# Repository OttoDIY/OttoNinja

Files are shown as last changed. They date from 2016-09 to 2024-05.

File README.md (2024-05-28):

# Otto Ninja Robot Arduino Libraries




This repository has the main [Otto Ninja robot](https://www.ottodiy.com/ninja) libraries for ESP compatible boards.

## Compatible Hardware

- Designed to work with ESP8266 boards, but most of the code could be adapted to other microcontrollers.

You will need to [add the ESP8266 to your Arduino IDE](https://randomnerdtutorials.com/how-to-install-esp8266-board-arduino-ide/)

:star: Star us on GitHub; it helps!

## Installation:

You will need the [Arduino IDE on your computer](https://www.arduino.cc/en/software)

1. [Download Otto Ninja libraries here](https://github.com/OttoDIY/OttoNinja/archive/master.zip)
2. Open the Arduino IDE and navigate to Sketch > Include Library > Add .ZIP Library...
3. Navigate to .zip file location that you just downloaded and open it.
4. You will see in the bottom black area a message that it has been installed. 
5. To verify they are properly installed, go to Sketch > Include Library menu. You should now see the library at the bottom of the drop-down menu.

## Example:

You can find codes in File > Examples > OttoNinja.

*For more details or other ways to [install libraries, visit this link](https://www.arduino.cc/en/Guide/Libraries) 

*For the LED matrix, you will need the [Adafruit LED Backpack library and all the dependencies](https://github.com/adafruit/Adafruit_LED_Backpack/archive/refs/heads/master.zip) just do the exact same installation steps.

*For the OLED display, you will need the [U8g2 libraries](https://github.com/olikraus/u8g2/archive/refs/heads/master.zip)

## Uploading:

For the firmware code to remote control Ninja via the [Remote XY mobile App](https://remotexy.com), select NodeMCU 1.0 as the board.

1. Connect the ESP board using the USB cable to your computer.

2. [Upload this code](https://github.com/OttoDIY/OttoNinja/blob/master/examples/App/OttoNinja_APP/OttoNinja_APP.ino) 
3. [Download the app to your phone](https://remotexy.com/en/download/)
4. Open the app and press + Add new device.
5. Select the WiFi point.
6. Select "OTTO NINJA" from the options.
7. The password is 12345678.

(Make sure to have wifi disconnected from other networks) and power the robot with a battery all the time.

## How to Contribute:
Contributing to this software is warmly welcomed.
1. Test it, and if you find any problems, then post an issue.
2. Help us solve the issues or other bugs.
3. Improve and optimize the current libraries.
You can do this [basically by forking](https://help.github.com/en/articles/fork-a-repo), committing modifications, and then [pull a request](https://help.github.com/en/articles/about-pull-requests). 

Thanks for your contribution, and welcome to the [Otto DIY community](https://www.ottodiy.com/community)

## License: CC-BY-SA
You can use all resources of Otto for free, but Otto DIY website must be included in any redistribution, and remixes must keep the CC-BY-SA license. In open source, the idea is that more people can have access; therefore, if you copy or remix Otto, you must also release it under the same open license, which means you must also release all files to the public.

<br /><span xmlns:dct="http://purl.org/dc/terms/" property="dct:title">Otto DIY</span> by <a xmlns:cc="http://creativecommons.org/ns#"  property="cc:attributionName"> [www.ottodiy.com](http://www.ottodiy.com) </a> is licensed under a <a rel="license" href="http://creativecommons.org/licenses/by-sa/4.0/">Creative Commons Attribution-ShareAlike 4.0 International License</a>.

Thanks to [Sebastian Coddington](https://github.com/SebastianCoddington) for this project.

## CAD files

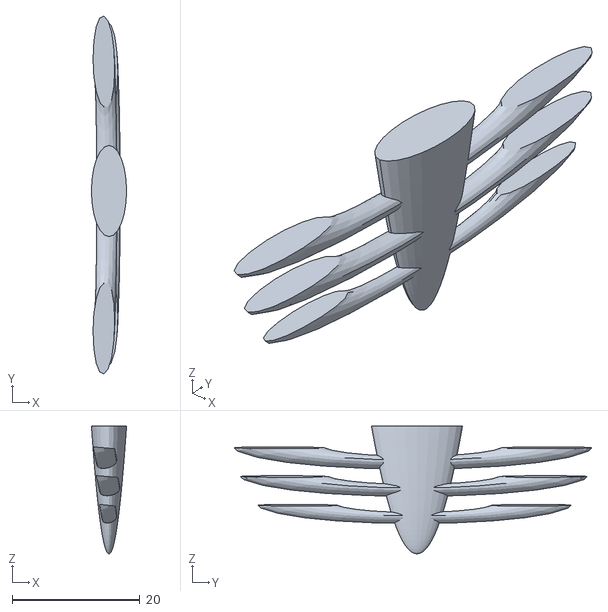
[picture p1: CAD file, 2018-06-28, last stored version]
3D print/accessories/Otto_RibCage.stl
5.50 x 56.0 x 20.0

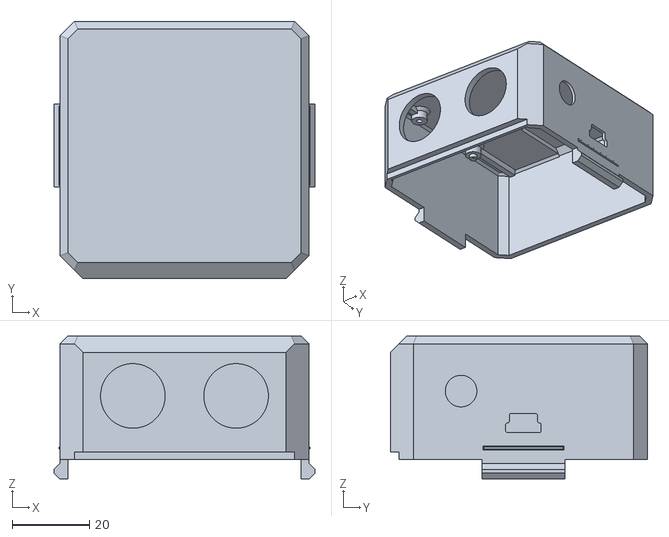
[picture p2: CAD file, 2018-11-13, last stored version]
3D print/OttoDIY+_head_v08.stl
67.6 x 66.7 x 37.0

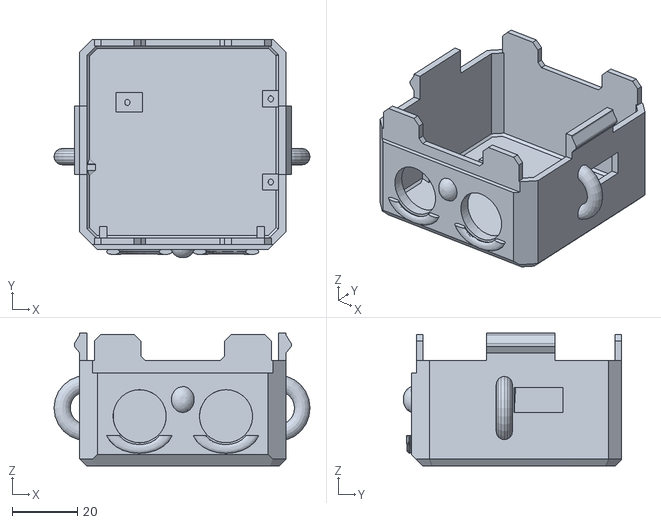
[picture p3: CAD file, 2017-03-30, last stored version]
OTTO_V02_BOM_STP_STL/Otto_Head+Face_Ears.stl
78.5 x 66.8 x 40.7

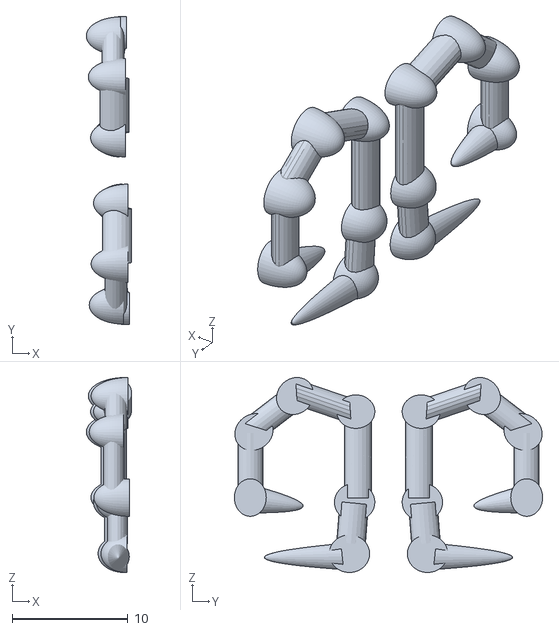
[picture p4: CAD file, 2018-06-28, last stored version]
3D print/accessories/Otto_BoneyHands.stl
3.92 x 26.6 x 16.8

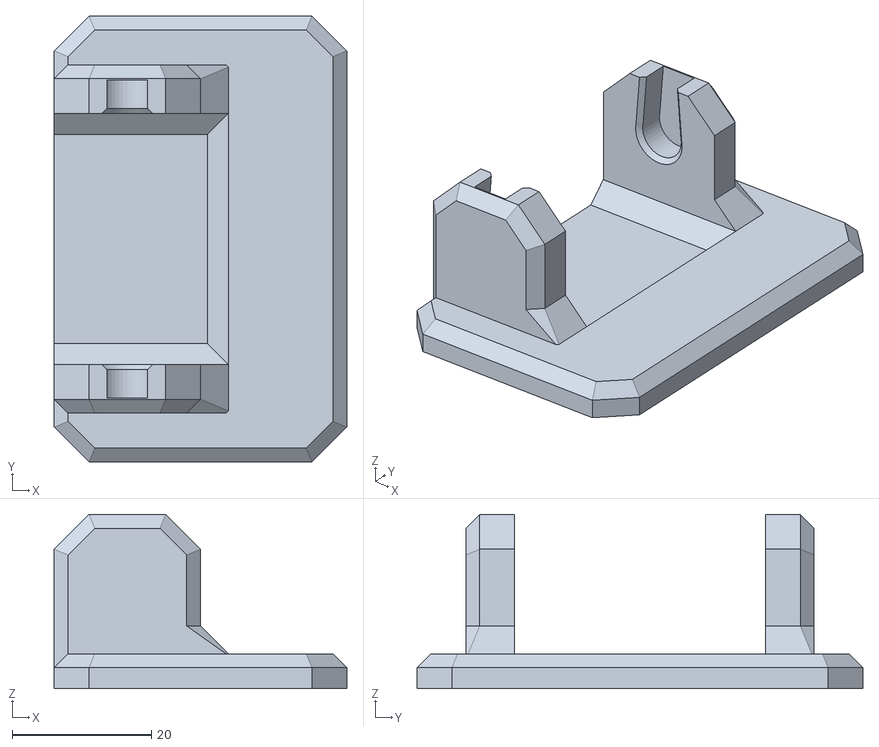
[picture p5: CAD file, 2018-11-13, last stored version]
3D print/OttoDIY+_foot_v08.stl
42.0 x 64.0 x 25.0

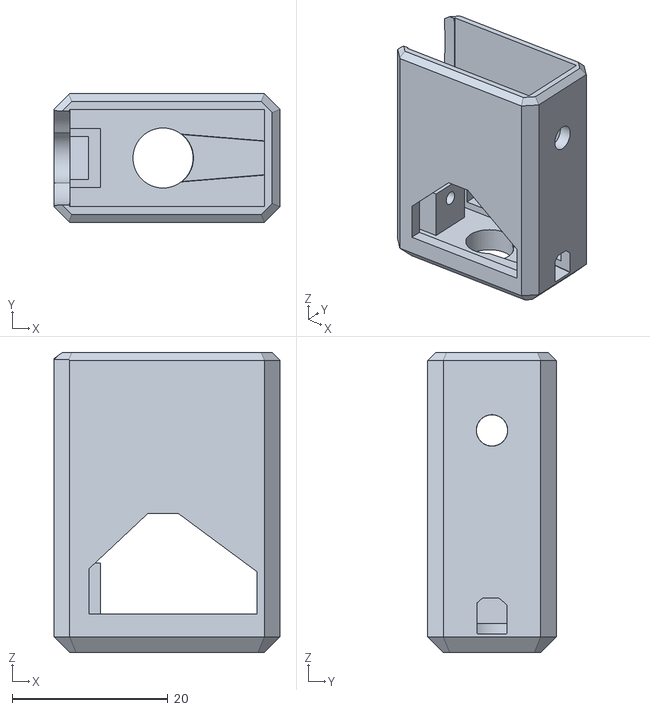
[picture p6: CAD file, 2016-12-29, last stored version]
OTTO_V02_BOM_STP_STL/OTTO_leg_v4.stl
29.0 x 16.5 x 38.5

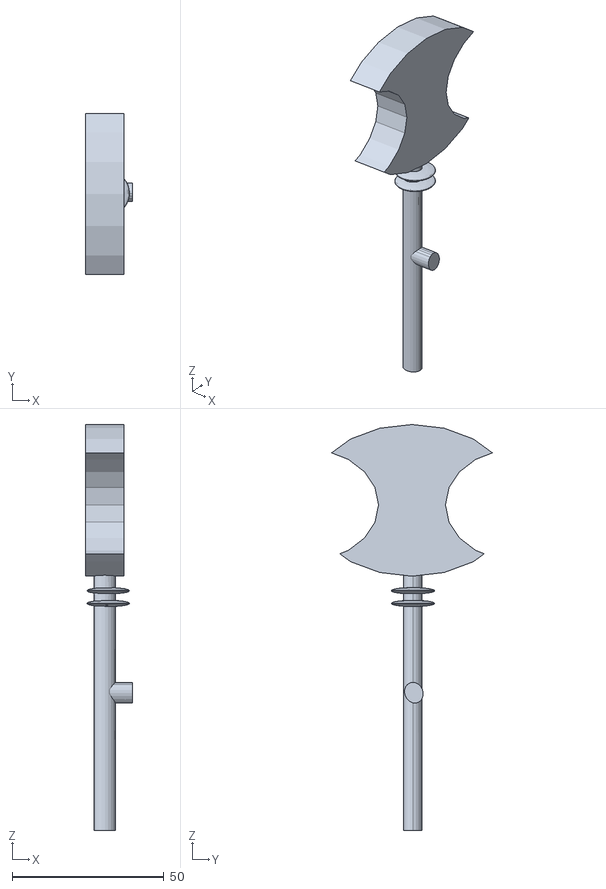
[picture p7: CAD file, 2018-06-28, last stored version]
3D print/accessories/Otto_MedievalAxe.stl
15.5 x 53.0 x 133.8

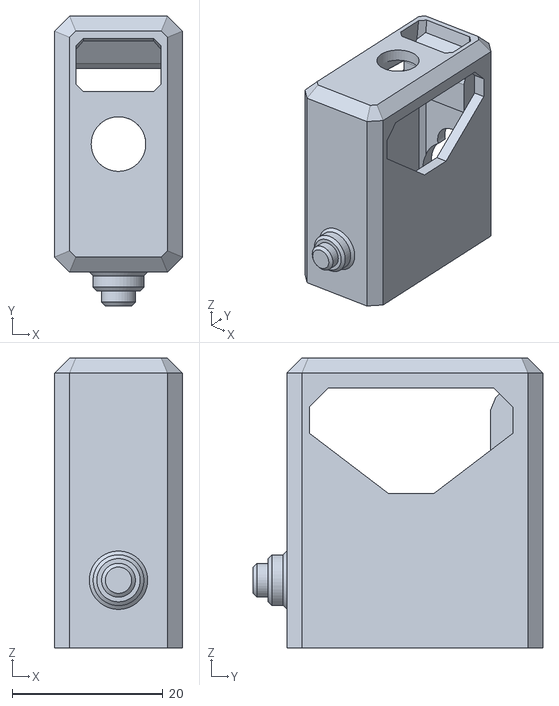
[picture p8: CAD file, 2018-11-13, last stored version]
3D print/OttoDIY+_Leg_v08.stl
17.0 x 38.5 x 38.5

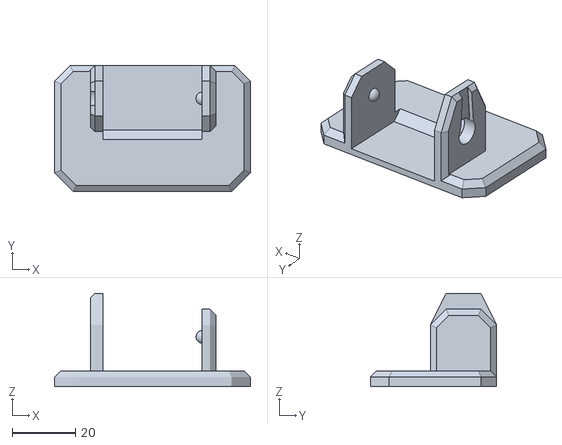
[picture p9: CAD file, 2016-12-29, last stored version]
OTTO_V02_BOM_STP_STL/OTTO_footR_v3.stl
62.0 x 40.0 x 29.5

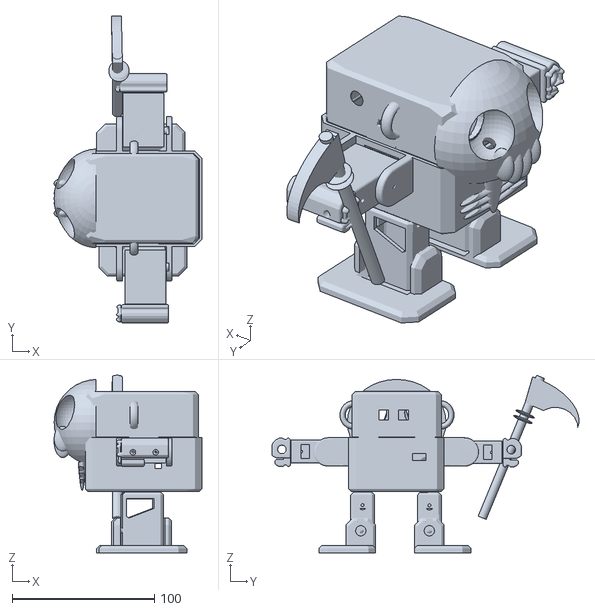
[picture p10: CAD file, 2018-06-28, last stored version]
3D print/accessories/Otto_Halloween_remix_Tinyplans_minion.stl
104.0 x 216.1 x 125.0

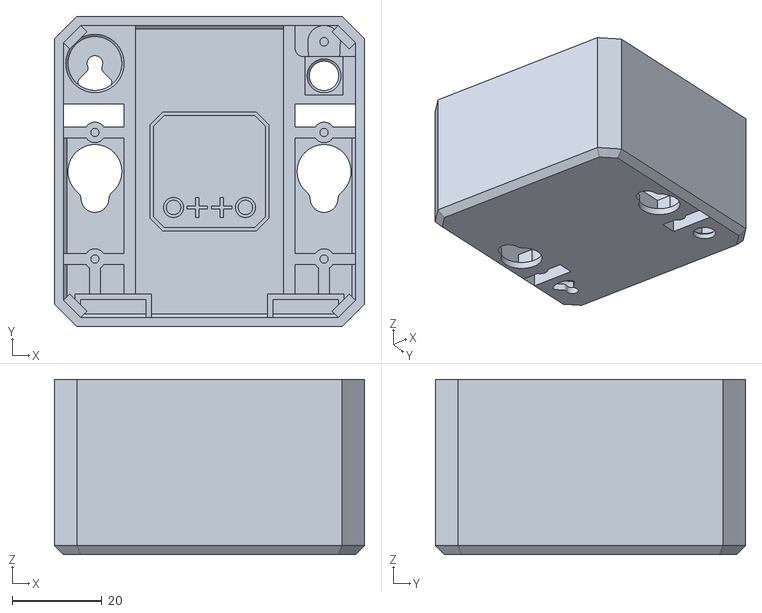
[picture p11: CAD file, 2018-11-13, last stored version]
3D print/OttoDIY+_body_v08.stl
69.0 x 69.0 x 39.0

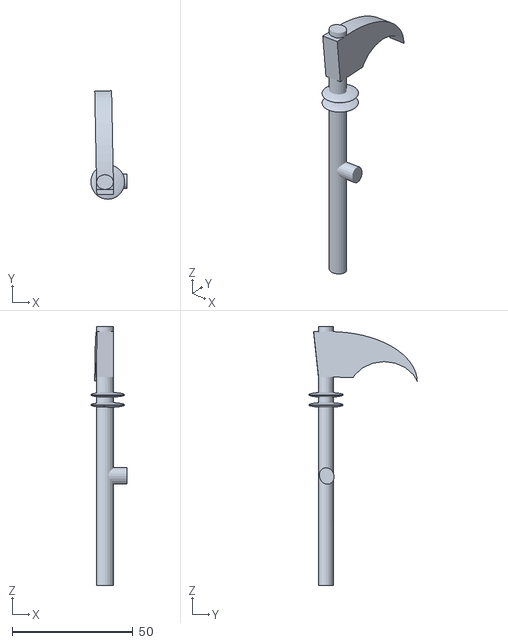
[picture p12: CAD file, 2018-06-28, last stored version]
3D print/accessories/Otto_Scythe+Connect.stl
15.0 x 45.0 x 107.4

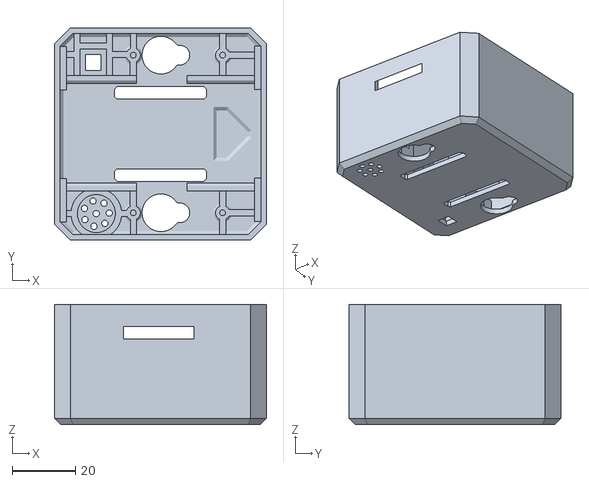
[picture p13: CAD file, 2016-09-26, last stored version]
OTTO_V02_BOM_STP_STL/OTTO_body_v3.stl
67.0 x 67.0 x 38.0

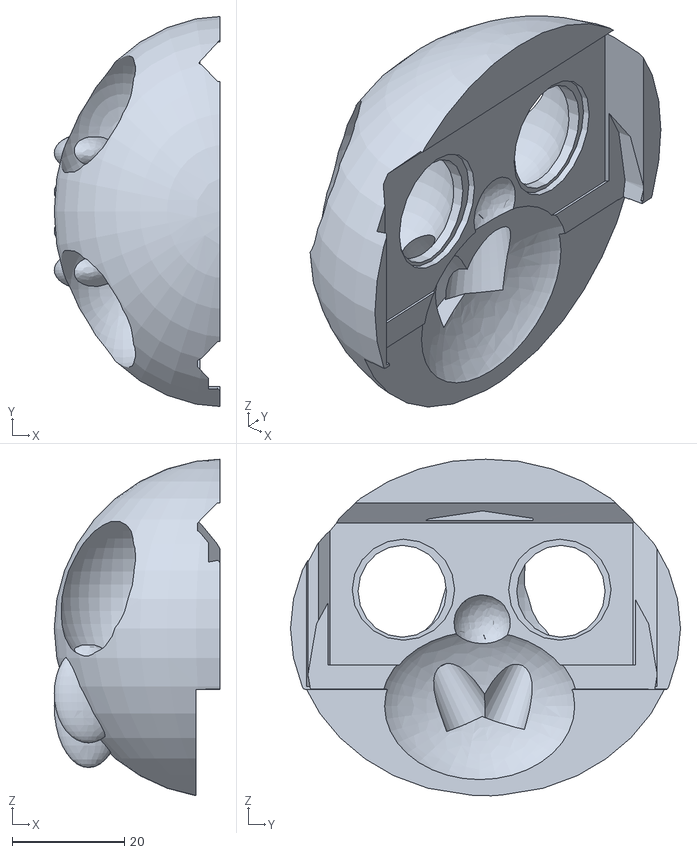
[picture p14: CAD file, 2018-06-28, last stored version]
3D print/accessories/Otto_Skull.stl
29.5 x 69.5 x 60.0

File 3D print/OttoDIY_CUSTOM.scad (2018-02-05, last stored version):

// Part to print
part="all"; // [all:Preview Bot,head:Head,body:Body,leg:Leg,foot_left:Left Foot,foot_right:Right Foot]

// Brain type (hole pattern in head)
brain_type="nano_shield"; // [nano_shield:Stock (Arduino Nano + Servo Shield),nano_proto:Arduino Nano + Proto board,uno_shield:Arduino Uno + Servo Shield,uno:Arduino Uno (and wires)]

// Servo Type for hip
servo_type_hip="sg90"; // [sg90:SG90 (nylon gear micro servo),mg90s:MG90S (metal gear micro servo)]

// Servo Type for ankle
servo_type_ankle="sg90"; // [sg90:SG90 (nylon gear micro servo),mg90s:MG90S (metal gear micro servo)]

// Body Width (Head width is based off this)
body_width=67; // [67:200]

// Body Depth (Head depth is based off this)
body_depth=68; // [68:200]

// Body Height
body_height=38; // [20:200]

// Head Height
head_height=34; // [20:200]

// Body Shell Thickness
body_thickness=1.75; // [0.25:0.25:8]

// Head Shell Thickness
head_thickness=2; // [0.25:0.25:8]

// Nose Diameter (6 = Small Toggle Switch)
nose_diameter=6; // [0:24]
// Vertical distance between center of eyes and nose
nose_distance=15; // [-8:190] 

// Brain Screw Size (2 = Stock)
brain_screw_size=2; // [2:5]

// Make Brain Screw thru Skull
brain_screw_thru=0; // [1:Yes,0:No]

// Solid leg
leg_solid=0; // [1:Yes, solid,0:No, my printer doesn't like those overhangs]

/* [Hidden] */
part_clearance=0.25;

arduino_holes=[[-27,-7],[-27,20.9],[25.2,26.1],[23.825,-22.25]];
proto_holes=[[27,-10],[-17.9,-10],[26,25.5],[-17.7,25.5]];

print_part();

module print_part() {
  warnings()
    draw_part();
}

module draw_part() {
  if(part=="head")
    head();
  else if(part=="body")
    body();
  else if(part=="leg")
    leg();
  else if(part=="foot_left")
    foot();
  else if(part=="foot_right")
    mirror([1,0]) foot();
  else if(part=="all")
    rotate([0,0,-90]) otto();
}
module otto() {
  head(move=1);
  body(move=1);
  mirrory() {
    translate([0,body_width/2-33.5,0])
    {
      mirror([1,0]) foot(move=1);
      translate([0,24,-1]) mirror([0,0,1]) leg(move=0);
    }
  }
}
function brain_type_text() = (
  brain_type=="nano_shield"?"Arduino Nano + Servo Shield":(
  brain_type=="uno_shield"?"Arduino Uno + Servo Shield":(
  brain_type=="nano_proto"?"Arduino Nano + Proto board":"Unknown")));
module warnings() {
  if(brain_type=="nano_shield")
  {
    if(body_width<67)
      error(str("If ",brain_type_text()," is used, Body Width must be >= 67!"));
    else if(body_depth<67)
      error(str("If ",brain_type_text()," is used, Body Depth must be >= 67!"));
    else children();
  } else if(brain_type=="uno_shield"||brain_type=="uno")
  {
    if(body_width<81)
      error("If Arduino Uno is used, body width MUST be greater than 81!");
    else children();
  } else children();
}
module error(s) {
  echo(str("***ERROR*** ",s));
  rotate([0,0,-45])
        rotate([80,0,0]) color("red") text(s);
}
module body(dims=[body_depth-1,body_width,body_height]) {
  left=dims[0]/-2; // -33.5
  botm=dims[1]/-2; // -33.5
  right=dims[0]/2; // 34
  servozoff=servo_type_hip=="sg90"?2:0;
  *#import("Otto_DIY/files/OTTO_body_v3.stl");
  mirrorx(0.4) mirrory(0.25) translate([left+body_thickness,botm+body_thickness+13.775,body_thickness]) {
      cube([dims[0]/2-9,2.5,12.4]);
      translate([0,2.5,12.39]) rotate([90,0,90]) mirror([1,0]) linear_extrude(dims[0]/2-9,convexity=10) polygon([[0,0],[1.2,0.825],[2.5,0.825],[2.5,0]]);
  }
  mirrory() mirrorx() translate([left+body_thickness-.01,botm+6,dims[2]-16]) difference(){
    cube([2,13.7,5]);
    translate([0,-.01]) rotate([0,41]) cube([3,13.72,5]);
  }
  mirrory() for(x=[0,28.2]) translate([x-9.5,botm+body_thickness,body_thickness]) difference() {
    union(){
      cube([2,13.775,6.18-servozoff]);
      translate([0.98,6.85,0]) cylinder(d1=5.7,d2=4.4,h=0.85,$fn=30);
      translate([0.98,6.85,0.84]) cylinder(d=4.4,h=5.35-servozoff,$fn=40);
    }
      translate([0.98,6.85,-.01]) cylinder(d=1.9,h=7,$fn=20);
  }
  for(mx=[0,1],my=[0,1]) mirror([mx,0]) mirror([0,my]) translate([mx?-11:0,0])
  translate([left+body_thickness+22.2,botm+body_thickness,body_thickness]) difference() { union() {
      if(!mx&&!my)
        translate([-10.7,6.61])
          cylinder(d=16,h=6.25-servozoff,$fn=50);
      else if(!mx&&my)
        translate([-17.5,0,.01]) cube([11.9,13.2,6-servozoff]);
      translate([-1-(left+33),5.64,0]) mirror([1,0]) cube([(mx?-22:-12)-left,2,6.1-servozoff]);
    }
    if(!mx&&!my)
      translate([-10.72,6.61,-.01]) cylinder(d=12,h=6.27,$fn=40);
    else if(!mx&&my)
      translate([-15.9,5,-.01]) {
        cube([8.35,8.2,7]);
        translate([0,-6]) cube([8.35,4,7]);
      }
  }
  difference() {
      translate([left,botm,0]) box_chamfer(dims,ch=2,chvx=5,chvy=5);
//    translate([left+1.75,botm+1.75,2]) box_chamfer([dims[0]-3.5,dims[1]-3.5,dims[2]],ch=1,chvx=4,chvy=4,inside=1);
    translate([left+body_thickness,botm+body_thickness,2]) box_chamfer([dims[0]-body_thickness*2,dims[1]-body_thickness*2,dims[2]],ch=1,chvx=4,chvy=4,inside=1);
    translate([0,0,-1]) linear_extrude(10,convexity=10) {
      mirrory() {
        translate([.1,botm+8.5]) circle(d=12,$fn=30);
        translate([6,botm+8.5]) circle(d=servo_type_hip=="mg90s"?6.5:7,$fn=20);
        offset(-1) offset(1)
        translate([-14.5,-15]) square([29,4]);
      }
      translate([left+9,-botm-13.5]) square([5.2,5.2]);
      translate([left+12.8,botm+8.35]) {
        circle(d=2,$fn=20);
        for(r=[2:360/7:359]) rotate([0,0,r]) translate([4.1,0]) circle(d=2,$fn=20);
      }
    }
    mirrory() translate([-11.7,right-body_thickness-.51,dims[2]-11]) {  cube([22.35,body_thickness+0.6,4]);
      translate([0,body_thickness+.02,4.1]) rotate([-35,0]) mirror([0,0,1]) mirror([0,1,0]) cube([22.35,4,5.4]);
    }
  }
}
module head(dims=[
    body_width-(body_thickness+part_clearance)*2,
    body_depth-(body_thickness+part_clearance)*2,
    head_height],brain_type=brain_type,head_thickness=head_thickness,move=0) {
  left=dims[0]/-2; // -31.5
  botm=dims[1]/-2; // -32.25
  right=dims[0]/2; // 31.5
  translate(move?[0,0,body_height+head_height-3]:[]) rotate(move?[180,0,-90]:[]) {
    //#import("Otto_DIY/files/OTTO_head_v3.stl");
    difference(){
      translate([left,botm,0]) box_chamfer(dims,ch=2,chy1=3.5,chvx=5.5,chvy=4);
      translate([left+head_thickness,botm+head_thickness+1.501,head_thickness]) box_chamfer([dims[0]-head_thickness*2,dims[1]-head_thickness*2-1.5,dims[2]],ch=1,chvx=2.75,chvy=2.75,inside=1);
      translate([left,botm-.01,dims[2]-3.8]) cube([dims[0],1.5,10]);
      for(x=[-13.25,13.25])
        translate([x,botm-.01,15]) rotate([-90,0]) cylinder(d=16.5,h=4,$fn=50);
      brain_holes(brain_type,top=dims[1]/2-20,right=dims[0]/2);
      translate([-5.6,-29.555,3.75]) {
        translate([11.25,0]) rotate([-90,0]) rotate([0,0,180]) intersection() {
          box_chamfer([11.3,7.6,2],ch=0,chvx=1.6,chvy=1.6);
          translate([0,0,-.8]) box_chamfer([11.3,7.6,4],ch=1.6,chvx=0,chvy=0);
          
        }
      }
      if(nose_diameter>0&&dims[2]-(nose_diameter/2+nose_distance)>18)
      {
        translate([0,botm-.01,15+nose_distance]) rotate([-90,0]) cylinder(d=nose_diameter,h=head_thickness+2.02,$fn=30);
      } else echo(str("Warning: Hiding nose."));
    }
    // tabs
    mirrorx() translate([-left-2,-9.25,dims[2]]) rotate([-90,0]) mirror([0,1,0]) linear_extrude(21,convexity=10) polygon([[0,0],[0,8.4],[1.98,8.4],[4.1,6.3],[4.1,4.2],[2,2.5],[2,0],]);
    mirrory(0.75) mirrorx(0) translate([left+4.5,botm+1.5,dims[2]]) rotate([90,0]) mirror([0,0,1]) linear_extrude(2) polygon([[0,0],[0,6],[2,8],[12,8],[14,6],[14,1.5],[15.5,0]]);
    brain(brain_type=brain_type,top=dims[1]/2-20,right=dims[0]/2);
  }
}
module leg(move=0) {
  bo=servo_type_ankle=="sg90"?0:(
    servo_type_ankle=="mg90s"?1.6:0);
  translate(move?[0,24,-40]:[]) rotate([0,0,0]) union(){
  //#import("Otto_DIY/files/OTTO_leg_v4.stl");
  difference() {
    translate([-14.5,-8.25,0]) {
      intersection() {
        cube([29,16.5,38.5]);
        union(){
          box_chamfer([29,16.5,20],2);
          translate([0,0,38.6]) mirror([0,0,1]) box_chamfer([29,16.5,20],1.25,chvx=2,chvy=2);
          *translate([1,1,30])
            box_chamfer2([29-2,16.5-2,7],2);
        }
      }
    }
    translate([-12.5,-6.25,4.25]) cube([25,12.5,50]);
    translate([12,-3,5]) cube([6,6,7.5]);
    translate([0.5,0,2.6-(servo_type_hip=="mg90s"?0:1)]) rotate([0,0,90]) {
      linear_extrude(3.4) 
        polygon([[-3.1,0],[-2,20],[2,20],[2.8,0]]); 
      translate([0,0,-3.01]) cylinder(d=servo_type_ankle=="mg90s"?7.8:7.4,h=8,$fn=30);
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

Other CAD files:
OTTO_V02_BOM_STP_STL/OTTO_footL_v3.stl
OTTO_V02_BOM_STP_STL/OTTO_head_v3.stl
3D print/accessories/Otto_Horns.stl
3D print/accessories/OttoDIY_Kitty.stl
3D print/OTTO_body_Pedro.stl
3D print/OTTO_feet_Pedro.stl
3D print/OTTO_footL_v4.stl
3D print/OTTO_footR_v4.stl
3D print/OTTO_head_Pedro.stl
3D print/OTTO_head_v3.stl
3D print/OTTO_leg_Pedro.stl
3D print/OTTO_leg_v4.stl
3D print/OttoDIY+_Leg_v07.stl
3D print/OttoDIY+_body_v07.stl
3D print/OttoDIY+_foot_v06.stl
3D print/OttoDIY+_head_v07.stl
3D print/OttoDIY_Feet_v05.stl
3D print/OttoDIY_Legs_v05.stl
3D print/OttoDIY_head_v3.stl
3D print/accessories/OttoDIY_AngryEyes.stl
3D print/accessories/OttoDIY_Bunny.stl
3D print/accessories/OttoDIY_Elf.stl
3D print/accessories/OttoDIY_Ninja.stl
3D print/accessories/OttoDIY_PumpkinMonster.stl
3D print/accessories/OttoDIY_Puppy.stl
3D print/accessories/OttoDIY_RockMonster.stl
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

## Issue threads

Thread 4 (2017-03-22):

Active or passive buzzer?

cmcoffman, 2017-03-22:
All the documentation I can find says I need a "5V buzzer" but it's not clear if this is supposed to be an _active_ or _passive_ buzzer. Links to ebay and amazon will have both, and they look similar.

The pictures look more like an active buzzer (which only is capable of producing one tone (I thinnk?), but I would think you would need a passive one.

I am unsure, any clarification?

cparrapa, 2017-03-23:
Hi is DC voltage so is an active buzzer.

cmcoffman, 2017-03-23:
Thanks!

Closed 2017-03-23.

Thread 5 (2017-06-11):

OTTO_calibration.ino won't compile / SerialUI

justinotherguy, 2017-06-11:
Hi,
first of all: thank you for this wonderful project! :)
I'd like to help improve - so here's a first issue report:
when I try to compile OTTO_calibration.ino I get a bunch of error messages (see below).
As far as I can tell, they seem to refer to SerialUI, which seems properly installed to me:

```
host:libraries justin$ ls -al SerialUI/
total 24
drwxr-xr-x   8 justin  staff   272  7 Jun 19:39 .
drwxr-xr-x  53 justin  staff  1802 11 Jun 09:07 ..
-rw-r--r--   1 justin  staff  3785 30 Nov  1979 README.md
drwxr-xr-x   4 justin  staff   136  7 Jun 19:39 examples
drwxr-xr-x   4 justin  staff   136  7 Jun 19:39 extras
-rw-r--r--   1 justin  staff  1256 30 Nov  1979 keywords.txt
-rw-r--r--   1 justin  staff   878 30 Nov  1979 library.properties
drwxr-xr-x  18 justin  staff   612  7 Jun 19:39 src
host:libraries justin$ pwd
/Users/justin/Documents/Arduino/libraries

```
Any idea, what I might be doing wrong?

My environment:
- Arduino 1.8.3 for OSX

Here's the output I get:
```
Arduino: 1.8.3 (Mac OS X), Board: "Arduino Nano, ATmega328"

/Users/justin/Documents/OttoDIY/OTTO_calibration/OTTO_calibration.ino: In function 'void setup()':
OTTO_calibration:102: error: no matching function for call to 'SUI::Menu::setName(const char [10])'
   mainMenu->setName(top_menu_title);
                                   ^
/Users/justin/Documents/OttoDIY/OTTO_calibration/OTTO_calibration.ino:102:35: note: candidate is:
In file included from /Users/justin/Documents/Arduino/libraries/SerialUI/src/includes/SerialUI.h:264:0,
                 from /Users/justin/Documents/Arduino/libraries/SerialUI/src/SerialUI.h:31,
                 from /Users/justin/Documents/OttoDIY/OTTO_calibration/OTTO_calibration.ino:24:
/Users/justin/Documents/Arduino/libraries/SerialUI/src/includes/SUIMenu.h:320:7: note: void SUI::Menu::setName(const __FlashStringHelper*)
  void setName(SOVA_FLASHSTRING_PTR namestr);
       ^
/Users/justin/Documents/Arduino/libraries/SerialUI/src/includes/SUIMenu.h:320:7: note:   no known conversion for argument 1 from 'const char [10]' to 'const __FlashStringHelper*'
OTTO_calibration:103: error: no matching function for call to 'SUI::Menu::subMenu(const char [3], const char [16])'
   SUI::Menu * laMenu = mainMenu->subMenu(la_key, la_help);
                                                         ^
/Users/justin/Documents/OttoDIY/OTTO_calibration/OTTO_calibration.ino:103:57: note: candidate is:
In file included from /Users/justin/Documents/Arduino/libraries/SerialUI/src/includes/SerialUI.h:264:0,
                 from /Users/justin/Documents/Arduino/libraries/SerialUI/src/SerialUI.h:31,
                 from /Users/justin/Documents/OttoDIY/OTTO_calibration/OTTO_calibration.ino:24:
/Users/justin/Documents/Arduino/libraries/SerialUI/src/includes/SUIMenu.h:308:9: note: SUI::Menu* SUI::Menu::subMenu(const __FlashStringHelper*, const __FlashStringHelper*)
  Menu * subMenu(SOVA_FLASHSTRING_PTR key_str, SOVA_FLASHSTRING_PTR help_str=NULL);
         ^
/Users/justin/Documents/Arduino/libraries/SerialUI/src/includes/SUIMenu.h:308:9: note:   no known conversion for argument 1 from 'const char [3]' to 'const __FlashStringHelper*'
OTTO_calibration:104: error: no matching function for call to 'SUI::Menu::addCommand(const char [2], void (&)(), const char [19])'
   laMenu->addCommand(la_plus_key, CB_leftAnklePlus, la_plus_help);
                                                                 ^
/Users/justin/Documents/OttoDIY/OTTO_calibration/OTTO_calibration.ino:104:65: note: candidate is:
In file included from /Users/justin/Documents/Arduino/libraries/SerialUI/src/includes/SerialUI.h:264:0,
                 from /Users/justin/Documents/Arduino/libraries/SerialUI/src/SerialUI.h:31,
                 from /Users/justin/Documents/OttoDIY/OTTO_calibration/OTTO_calibration.ino:24:
/Users/justin/Documents/Arduino/libraries/SerialUI/src/includes/SUIMenu.h:100:7: note: bool SUI::Menu::addCommand(const __FlashStringHelper*, SUI::MenuCommand_Callback, const __FlashStringHelper*)
  bool addCommand(SOVA_FLASHSTRING_PTR key_str, MenuCommand_Callback callback,SOVA_FLASHSTRING_PTR help_str=NULL);
       ^
/Users/justin/Documents/Arduino/libraries/SerialUI/src/includes/SUIMenu.h:100:7: note:   no known conversion for argument 1 from 'const char [2]' to 'const __FlashStringHelper*'
OTTO_calibration:105: error: no matching function for call to 'SUI::Menu::addCommand(const char [2], void (&)(), const char [19])'
   laMenu->addCommand(la_minus_key, CB_leftAnkleMinus, la_minus_help);
                                                                    ^
/Users/justin/Documents/OttoDIY/OTTO_calibration/OTTO_calibration.ino:105:68: note: candidate is:
In file included from /Users/justin/Documents/Arduino/libraries/SerialUI/src/includes/SerialUI.h:264:0,
                 from /Users/justin/Documents/Arduino/libraries/SerialUI/src/SerialUI.h:31,
                 from /Users/justin/Documents/OttoDIY/OTTO_calibration/OTTO_calibration.ino:24:
/Users/justin/Documents/Arduino/libraries/SerialUI/src/includes/SUIMenu.h:100:7: note: bool SUI::Menu::addCommand(const __FlashStringHelper*, SUI::MenuCommand_Callback, const __FlashStringHelper*)
  bool addCommand(SOVA_FLASHSTRING_PTR key_str, MenuCommand_Callback callback,SOVA_FLASHSTRING_PTR help_str=NULL);
       ^
/Users/justin/Documents/Arduino/libraries/SerialUI/src/includes/SUIMenu.h:100:7: note:   no known conversion for argument 1 from 'const char [2]' to 'const __FlashStringHelper*'
OTTO_calibration:106: error: no matching function for call to 'SUI::Menu::subMenu(const char [3], const char [17])'
   SUI::Menu * raMenu = mainMenu->subMenu(ra_key, ra_help);
                                                         ^
/Users/justin/Documents/OttoDIY/OTTO_calibration/OTTO_calibration.ino:106:57: note: candidate is:
In file included from /Users/justin/Documents/Arduino/libraries/SerialUI/src/includes/SerialUI.h:264:0,
                 from /Users/justin/Documents/Arduino/libraries/SerialUI/src/SerialUI.h:31,
                 from /Users/justin/Documents/OttoDIY/OTTO_calibration/OTTO_calibration.ino:24:
/Users/justin/Documents/Arduino/libraries/SerialUI/src/includes/SUIMenu.h:308:9: note: SUI::Menu* SUI::Menu::subMenu(const __FlashStringHelper*, const __FlashStringHelper*)
  Menu * subMenu(SOVA_FLASHSTRING_PTR key_str, SOVA_FLASHSTRING_PTR help_str=NULL);
         ^
/Users/justin/Documents/Arduino/libraries/SerialUI/src/includes/SUIMenu.h:308:9: note:   no known conversion for argument 1 from 'const char [3]' to 'const __FlashStringHelper*'
OTTO_calibration:107: error: no matching function for call to 'SUI::Menu::addCommand(const char [2], void (&)(), const char [20])'
   raMenu->addCommand(ra_plus_key, CB_rightAnklePlus, ra_plus_help);
                                                                  ^
/Users/justin/Documents/OttoDIY/OTTO_calibration/OTTO_calibration.ino:107:66: note: candidate is:
In file included from /Users/justin/Documents/Arduino/libraries/SerialUI/src/includes/SerialUI.h:264:0,
                 from /Users/justin/Documents/Arduino/libraries/SerialUI/src/SerialUI.h:31,
                 from /Users/justin/Documents/OttoDIY/OTTO_calibration/OTTO_calibration.ino:24:
/Users/justin/Documents/Arduino/libraries/SerialUI/src/includes/SUIMenu.h:100:7: note: bool SUI::Menu::addCommand(const __FlashStringHelper*, SUI::MenuCommand_Callback, const __FlashStringHelper*)
  bool addCommand(SOVA_FLASHSTRING_PTR key_str, MenuCommand_Callback callback,SOVA_FLASHSTRING_PTR help_str=NULL);
       ^
/Users/justin/Documents/Arduino/libraries/SerialUI/src/includes/SUIMenu.h:100:7: note:   no known conversion for argument 1 from 'const char [2]' to 'const __FlashStringHelper*'
OTTO_calibration:108: error: no matching function for call to 'SUI::Menu::addCommand(const char [2], void (&)(), const char [20])'
   raMenu->addCommand(ra_minus_key, CB_rightAnkleMinus, ra_minus_help);
                                                                     ^
/Users/justin/Documents/OttoDIY/OTTO_calibration/OTTO_calibration.ino:108:69: note: candidate is:
In file included from /Users/justin/Documents/Arduino/libraries/SerialUI/src/includes/SerialUI.h:264:0,
                 from /Users/justin/Documents/Arduino/libraries/SerialUI/src/SerialUI.h:31,
                 from /Users/justin/Documents/OttoDIY/OTTO_calibration/OTTO_calibration.ino:24:
/Users/justin/Documents/Arduino/libraries/SerialUI/src/includes/SUIMenu.h:100:7: note: bool SUI::Menu::addCommand(const __FlashStringHelper*, SUI::MenuCommand_Callback, const __FlashStringHelper*)
  bool addCommand(SOVA_FLASHSTRING_PTR key_str, MenuCommand_Callback callback,SOVA_FLASHSTRING_PTR help_str=NULL);
       ^
/Users/justin/Documents/Arduino/libraries/SerialUI/src/includes/SUIMenu.h:100:7: note:   no known conversion for argument 1 from 'const char [2]' to 'const __FlashStringHelper*'
OTTO_calibration:109: error: no matching function for call to 'SUI::Menu::subMenu(const char [3], const char [14])'
   SUI::Menu * lhMenu = mainMenu->subMenu(lh_key, lh_help);
                                                         ^
/Users/justin/Documents/OttoDIY/OTTO_calibration/OTTO_calibration.ino:109:57: note: candidate is:
In file included from /Users/justin/Documents/Arduino/libraries/SerialUI/src/includes/SerialUI.h:264:0,
                 from /Users/justin/Documents/Arduino/libraries/SerialUI/src/SerialUI.h:31,
                 from /Users/justin/Documents/OttoDIY/OTTO_calibration/OTTO_calibration.ino:24:
/Users/justin/Documents/Arduino/libraries/SerialUI/src/includes/SUIMenu.h:308:9: note: SUI::Menu* SUI::Menu::subMenu(const __FlashStringHelper*, const __FlashStringHelper*)
  Menu * subMenu(SOVA_FLASHSTRING_PTR key_str, SOVA_FLASHSTRING_PTR help_str=NULL);
         ^
/Users/justin/Documents/Arduino/libraries/SerialUI/src/includes/SUIMenu.h:308:9: note:   no known conversion for argument 1 from 'const char [3]' to 'const __FlashStringHelper*'
OTTO_calibration:110: error: no matching function for call to 'SUI::Menu::addCommand(const char [2], void (&)(), const char [17])'
   lhMenu->addCommand(lh_plus_key, CB_leftHipPlus, lh_plus_help);
                                                               ^
/Users/justin/Documents/OttoDIY/OTTO_calibration/OTTO_calibration.ino:110:63: note: candidate is:
In file included from /Users/justin/Documents/Arduino/libraries/SerialUI/src/includes/SerialUI.h:264:0,
                 from /Users/justin/Documents/Arduino/libraries/SerialUI/src/SerialUI.h:31,
                 from /Users/justin/Documents/OttoDIY/OTTO_calibration/OTTO_calibration.ino:24:
/Users/justin/Documents/Arduino/libraries/SerialUI/src/includes/SUIMenu.h:100:7: note: bool SUI::Menu::addCommand(const __FlashStringHelper*, SUI::MenuCommand_Callback, const __FlashStringHelper*)
  bool addCommand(SOVA_FLASHSTRING_PTR key_str, MenuCommand_Callback callback,SOVA_FLASHSTRING_PTR help_str=NULL);
       ^
/Users/justin/Documents/Arduino/libraries/SerialUI/src/includes/SUIMenu.h:100:7: note:   no known conversion for argument 1 from 'const char [2]' to 'const __FlashStringHelper*'
OTTO_calibration:111: error: no matching function for call to 'SUI::Menu::addCommand(const char [2], void (&)(), const char [17])'
   lhMenu->addCommand(lh_minus_key, CB_leftHipMinus, lh_minus_help);
                                                                  ^
/Users/justin/Documents/OttoDIY/OTTO_calibration/OTTO_calibration.ino:111:66: note: candidate is:
In file included from /Users/justin/Documents/Arduino/libraries/SerialUI/src/includes/SerialUI.h:264:0,
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
hulkco, 2017-06-11:
Hi, try a old version of the IDE 1.6.X

justinotherguy, 2017-06-11:
Yep - using an old version of SerialUI helps! :)
I've downgraded SerialUI to 1.14.0 and now it works; versions 2.1.2 and 2.1.4 cause the above behaviour.
So - thx! Closing the issue as solved!

Closed 2017-06-11.

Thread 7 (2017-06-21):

STL files in repo

justinotherguy, 2017-06-21:
Hi,

I think it would be nice to have the STL files directly in the github repo and not within the Zip file.
This way people would be able to see straight away, whether the STL files have changed.

The difference between two versions can not be made visible - but it would be easier to track the changes.

What do you think?

Regards, J.

cparrapa, 2017-06-21:
Good idea i will add the stl files too so we people can rotate and see how they are like in thingiverse.

Closed 2017-06-21.

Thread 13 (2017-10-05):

How do I get my calibration to save to EEPROM

rskissel, 2017-10-05:
Hello,

I cannot get my changes to save to the EEPROM.
I can make the adjustments and then "save", then "quit".

However, when I run another program the settings seem to have disappeared and Otto's ankles and hips have reverted to the positions they were in prior to calibration.

Thanks for the help!

cparrapa, 2017-10-20:
Hi @rskissel just uploaded this week easycal give a try to that code

Closed 2017-10-20.

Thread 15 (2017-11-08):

_O defined as unsigned int in Oscillator.h

sushicodeur, 2017-11-08:
Hello,

I'm trying to make Otto work on my Esp8266.

It works quite well so far except for some very strange behaviors on oscillateServos function. For example if I run `Otto.updown(6, 500, BIG);` the right foot is totally up.

After some investigation it looks like for this function O is `int O[4] = {0, 0, h, -h};` so if you call updown with BIG you end up with these values `{0,0, 30, -30}`.

So far so good (well on arduino at last).

But on my ESP as _O is declared unsigned it takes 4,294,967,295 as a value... too much for my servo :)

So my question is : is it normal that _O is declared unsigned or is it a bug in Oscillator.h ?

cparrapa, 2017-11-09:
Hello
Awesome finally someone will make it!
hmmmm that value is to high maybe is a bug that wasn't noticeable in Arduino

Thanks!
Welcome to the Otto builder community!

sushicodeur, 2017-11-09:
I can confirm that changing the way _O is declared fixed the problem on my Esp Otto silly walk...

I now move on with the rest of the sketches and some more fun :)

I forked the repo here : https://github.com/sushicodeur/OttoOnEsp

cparrapa, 2017-11-10:
Great thanks! feel free to pull a request with a new folder or something i will just approve

sushicodeur, 2017-11-10:
I wait for my arduino nano to ship with ultrasonic sensor and shield, so I can test that my changes don't break on arduino.

cparrapa, 2017-11-10:
sure thanks for contributing! ;D

cparrapa, 2018-03-20:
Hey how is it going so is possible ESP with Otto?

Closed 2018-05-10.

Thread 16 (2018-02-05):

Error when uploading

Kenzieen, 2018-02-05:
Hi,

thats a newbie question, but every time I want to upload for example Otto_avoid - I got this error:

use of deleted function 'Otto::Otto()'

C:\Program Files (x86)\Arduino\libraries\Otto/Otto.h:32:7: note: 'Otto::Otto()' is implicitly deleted because the default definition would be ill-formed:

 class Otto

       ^

C:\Program Files (x86)\Arduino\libraries\Otto/Otto.h:32:7: error: no matching function for call to 'LedMatrix::LedMatrix()'

C:\Program Files (x86)\Arduino\libraries\Otto/Otto.h:32:7: note: candidates are:

In file included from C:\Program Files (x86)\Arduino\libraries\Otto/Otto.h:9:0,

                 from F:\Puplit\OTTO\Otto_BASIC\Otto_BASIC.ino:12:

C:\Program Files (x86)\Arduino\libraries\MAX7219LedMatrix-master/LedMatrix.h:33:5: note: LedMatrix::LedMatrix(byte, byte)

     LedMatrix(byte numberOfDisplays, byte slaveSelectPin);

     ^

C:\Program Files (x86)\Arduino\libraries\MAX7219LedMatrix-master/LedMatrix.h:33:5: note:   candidate expects 2 arguments, 0 provided

C:\Program Files (x86)\Arduino\libraries\MAX7219LedMatrix-master/LedMatrix.h:24:7: note: LedMatrix::LedMatrix(const LedMatrix&)

 class LedMatrix {

       ^

C:\Program Files (x86)\Arduino\libraries\MAX7219LedMatrix-master/LedMatrix.h:24:7: note:   candidate expects 1 argument, 0 provided

C:\Program Files (x86)\Arduino\libraries\MAX7219LedMatrix-master/LedMatrix.h:24:7: note: LedMatrix::LedMatrix(LedMatrix&&)

C:\Program Files (x86)\Arduino\libraries\MAX7219LedMatrix-master/LedMatrix.h:24:7: note:   candidate expects 1 argument, 0 provided

exit status 1
use of deleted function 'Otto::Otto()'

Could You help me ?

cparrapa, 2018-02-12:
try the other avoids, update your libraries

Closed 2018-02-12.

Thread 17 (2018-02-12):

LedMatrix lib is missing.

crazyquark, 2018-02-12:
LedMatrix lib is needed to build the project even though it is no longer included.
As a workaround I pulled it from the zowiLibs repo.

cparrapa, 2018-02-12:
hi Quark
is not missing is just in other repository the one call Matrix arms, because for this simple Otto DIY want to foucs on the basic build

Closed 2018-02-13.

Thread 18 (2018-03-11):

Missing LedMatrix.h

Pawka, 2018-03-11:
Compiling `Otto.h` file fails as `LedMatrix.h` is missing.

I haven't found this library anywhere on the repo and somewhere else. This might be an old library which was shipped with older Arduino IDE installations, but I was not able to find it there too.

Arduino IDE version: 1.8.5
Failing on: Otto.h:9 (`#include <LedMatrix.h>`)
OS: Ubuntu 16.04.4 LTS

## Workaround
As quick workaround would be disabling all calls to `LedMatrix` library.
After installing "Otto.zip" library, edit `Otto.h` and `Otto.cpp` files on  ~/Arduino/libraries/Otto/:

```diff
diff --git a/Otto.cpp b/Otto.cpp
index 2fa49f1..67bea9c 100644
--- a/Otto.cpp
+++ b/Otto.cpp
@@ -674,24 +674,24 @@ unsigned long int Otto::getAnimShape(int anim, int index){

 void Otto::putAnimationMouth(unsigned long int aniMouth, int index){

-      ledmatrix.writeFull(getAnimShape(aniMouth,index));
+      /* ledmatrix.writeFull(getAnimShape(aniMouth,index)); */
 }

 void Otto::putMouth(unsigned long int mouth, bool predefined){

   if (predefined){
-    ledmatrix.writeFull(getMouthShape(mouth));
+    /* ledmatrix.writeFull(getMouthShape(mouth)); */
   }
   else{
-    ledmatrix.writeFull(mouth);
+    /* ledmatrix.writeFull(mouth); */
   }
 }

 void Otto::clearMouth(){

-  ledmatrix.clearMatrix();
+  /* ledmatrix.clearMatrix(); */
 }

diff --git a/Otto.h b/Otto.h
index 7ed6116..2ce4018 100644
--- a/Otto.h
+++ b/Otto.h
@@ -6,7 +6,7 @@
 #include <EEPROM.h>

 #include <US.h>
-#include <LedMatrix.h>
+/* #include <LedMatrix.h> */
 #include <BatReader.h>

 #include "Otto_mouths.h"
@@ -95,7 +95,7 @@ class Otto

   private:

-    LedMatrix ledmatrix;
+    /* LedMatrix ledmatrix; */
     BatReader battery;
     Oscillator servo[4];
     US us;
```

### Update
I've just found LedMatrix code here: https://github.com/OttoDIY/Matrix_hands/tree/master/libraries/LedMatrix

cparrapa, 2018-03-20:
is ok we moved to another repository this is the basic entry Otto to make the code more simple

Pawka, 2018-03-20:
@cparrapa In the first place I want to thank you for building and maintaining Otto!

You mentioned this repository is supposed to be an entry level for early beginners. Currently it can not be this entry level as people simply can not compile it. And it can act even in an opposite way - early beginners will be pushed off once they'll see they can not compile "entry level" repository.
When I was building the Otto, I searched how to solve this problem. What I've found was only complains that people can not make it work (e.g. see comments here): http://www.instructables.com/id/Otto-Build-You-Own-Robot-in-Two-Hours/

I see two ways to solve this:
- If this repository is outdated and not supposed to work, I'd suggest putting a note at the top of README.md and mention that original repository is somewhere else and this one is outdated.
- If current repository is supposed to work - make sure people can compile it. This can be done by merging #19 PR or refactoring code to get rid of `LetMatrix`.

Pawka, 2018-03-20:
Thank you for merging!

If LedMatrix is not used under this repo I will be glad to help you and
remove that unnecessary code. Just let me know.

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

--
  .^.   Povilas Balzaravičius
  /V\   Software Engineer at Uber Technologies
 /(_)\  phone: +37060117345
  ^ ^   github.com/Pawka * twitter.com/Pawka

cparrapa, 2018-03-20:
Thanks to you! we need more Otto builders like you, able to put some order to this repositories many bugs around and we are also testing new codes that need to be verified.

just pull requests for similar bugs and in that way we keep track of the changes

Closed 2018-03-20.

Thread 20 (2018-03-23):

ledmatrix library

pedrito12, 2018-03-23:
Hola,
Esto construyendo el robot otto
Acabo de descargar la librería ledmatrix y la he puesto en el directorio de librerías para arduino.
A la hora de compilar en la IDE de arduino 1.8.5 los programas para manejar el robot, por ejemplo el siguiente

#include <Oscillator.h>

#include <Otto.h>
#include <Otto_gestures.h>
#include <Otto_mouths.h>
#include <Otto_sounds.h>

void setup() {
  // put your setup code here, to run once:

}

void loop() {
  // put your main code here, to run repeatedly:

}

Me sale el siguiente error

In file included from C:\Users\Pedro\Documents\Arduino\sketch_mar23a\sketch_mar23a.ino:3:0:

C:\Users\Pedro\Documents\Arduino\libraries\Otto/Otto.h:97:5: error: 'LedMatrix' does not name a type

     LedMatrix ledmatrix;

     ^

exit status 1
Error compilando para la tarjeta Arduino/Genuino Uno.

Este error me sale en otros programas como Otto_avoid_mhs.ino usan la libreria Otto.h.

¿como puedo solucionarlo?

Atentamente

Pedro

pedrito12, 2018-03-23:
Tambien he añadido las restantes librerias

Pedro

pedrito12, 2018-03-23:
Corregido problema leyendo los comentarios anteriores

Closed 2018-03-23.

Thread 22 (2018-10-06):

"Otto was not declared in this scope"

EddieMontana, 2018-10-06:
I recently made the Otto Robot. I was able to upload "Smooth criminal" and "Single ladies" in the Nano controller of the two robots.

However, as of Oct 6, 2018 all other .ino files (e.g. Otto_avoid, Run_Otto_Run, Otto_avoid_TRIMS, Otto_push, etc) within the Otto_DIY folder do not compile well and give an error of the type "Otto was not declared in this scope".
I have no idea what creates this error or whether it's a library, or the code itself for these files.
Below is a copy paste of the issue. Thank you!

Arduino: 1.8.6 (Windows 10), Board: "Arduino Nano, ATmega328P (Old Bootloader)"

In file included from C:\Users\Eddie & Tina\Desktop\OTTO_avoid\OTTO_avoid.ino:15:0:

C:\Program Files (x86)\Arduino\libraries\Otto/Otto.h:32:3: error: stray '\302' in program

   <title>DIY/Otto.h at master Â· OttoDIY/DIY Â· GitHub</title>

   ^

C:\Program Files (x86)\Arduino\libraries\Otto/Otto.h:32:3: error: stray '\267' in program

C:\Program Files (x86)\Arduino\libraries\Otto/Otto.h:32:3: error: stray '\302' in program

C:\Program Files (x86)\Arduino\libraries\Otto/Otto.h:32:3: error: stray '\267' in program

In file included from C:\Users\Eddie & Tina\Desktop\OTTO_avoid\OTTO_avoid.ino:15:0:

C:\Program Files (x86)\Arduino\libraries\Otto/Otto.h:170:10: warning: missing terminating ' character

     <!-- '"` --><!-- </textarea></xmp> --></option></form><form class="js-site-search-form" data-scope-type="Repository" data-scope-id="64104078" data-scoped-search-url="/OttoDIY/DIY/search" data-unscoped-search-url="/search" action="/OttoDIY/DIY/search" accept-charset="UTF-8" method="get"><input name="utf8" type="hidden" value="&#x2713;" />

          ^

C:\Program Files (x86)\Arduino\libraries\Otto/Otto.h:170:5: error: missing terminating ' character

     <!-- '"` --><!-- </textarea></xmp> --></option></form><form class="js-site-search-form" data-scope-type="Repository" data-scope-id="64104078" data-scoped-search-url="/OttoDIY/DIY/search" data-unscoped-search-url="/search" action="/OttoDIY/DIY/search" accept-charset="UTF-8" method="get"><input name="utf8" type="hidden" value="&#x2713;" />

     ^

In file included from C:\Users\Eddie & Tina\Desktop\OTTO_avoid\OTTO_avoid.ino:15:0:

C:\Program Files (x86)\Arduino\libraries\Otto/Otto.h:212:23: error: stray '\342' in program

                       <span aria-hidden="true" class="d-inline-block ml-1 v-align-middle">â†µ</span>

                       ^

C:\Program Files (x86)\Arduino\libraries\Otto/Otto.h:212:23: error: stray '\206' in program

C:\Program Files (x86)\Arduino\libraries\Otto/Otto.h:212:23: error: stray '\265' in program

C:\Program Files (x86)\Arduino\libraries\Otto/Otto.h:217:23: error: stray '\342' in program

                       <span class="d-inline-block ml-1 v-align-middle">â†µ</span>

                       ^

C:\Program Files (x86)\Arduino\libraries\Otto/Otto.h:217:23: error: stray '\206' in program

C:\Program Files (x86)\Arduino\libraries\Otto/Otto.h:217:23: error: stray '\265' in program

In file included from C:\Users\Eddie & Tina\Desktop\OTTO_avoid\OTTO_avoid.ino:15:0:

C:\Program Files (x86)\Arduino\libraries\Otto/Otto.h:393:16: warning: missing terminating ' character

           <!-- '"` --><!-- </textarea></xmp> --></option></form><form action="/site/dismiss_signup_prompt" accept-charset="UTF-8" method="post"><input name="utf8" type="hidden" value="&#x2713;" /><input type="hidden" name="authenticity_token" value="1Wemr0LMQpZmxIMEtdzLYnabHTduUMQ5eLwbI0PIIU6f/rgCg/lETMDHvH3y6obX/1v5lqgKXyoLDxMVhHQAYQ==" />

                ^

C:\Program Files (x86)\Arduino\libraries\Otto/Otto.h:393:11: error: missing terminating ' character

           <!-- '"` --><!-- </textarea></xmp> --></option></form><form action="/site/dismiss_signup_prompt" accept-charset="UTF-8" method="post"><input name="utf8" type="hidden" value="&#x2713;" /><input type="hidden" name="authenticity_token" value="1Wemr0LMQpZmxIMEtdzLYnabHTduUMQ5eLwbI0PIIU6f/rgCg/lETMDHvH3y6obX/1v5lqgKXyoLDxMVhHQAYQ==" />

           ^

In file included from C:\Users\Eddie & Tina\Desktop\OTTO_avoid\OTTO_avoid.ino:15:0:

C:\Program Files (x86)\Arduino\libraries\Otto/Otto.h:523:11: warning: floating constant exceeds range of 'double' [-Woverflow]

           9e38697

           ^

In file included from C:\Users\Eddie & Tina\Desktop\OTTO_avoid\OTTO_avoid.ino:15:0:

C:\Program Files (x86)\Arduino\libraries\Otto/Otto.h:614:69: error: stray '#' in program

         <td id="LC1" class="blob-code blob-code-inner js-file-line">#<span class="pl-k">ifndef</span> Otto_h</td>

                                                                     ^

C:\Program Files (x86)\Arduino\libraries\Otto/Otto.h:618:69: error: stray '#' in program

         <td id="LC2" class="blob-code blob-code-inner js-file-line">#<span class="pl-k">define</span> <span class="pl-en">Otto_h</span></td>

                                                                     ^

C:\Program Files (x86)\Arduino\libraries\Otto/Otto.h:627:69: error: stray '#' in program

         <td id="LC4" class="blob-code blob-code-inner js-file-line">#<span class="pl-k">include</span> <span class="pl-s"><span class="pl-pds">&lt;</span>Servo.h<span class="pl-pds">&gt;</span></span></td>

                                                                     ^

C:\Program Files (x86)\Arduino\libraries\Otto/Otto.h:631:69: error: stray '#' in program

         <td id="LC5" class="blob-code blob-code-inner js-file-line">#<span class="pl-k">include</span> <span class="pl-s"><span class="pl-pds">&lt;</span>Oscillator.h<span class="pl-pds">&gt;</span></span></td>

                                                                     ^

C:\Program Files (x86)\Arduino\libraries\Otto/Otto.h:635:69: error: stray '#' in program

         <td id="LC6" class="blob-code blob-code-inner js-file-line">#<span class="pl-k">include</span> <span class="pl-s"><span class="pl-pds">&lt;</span>EEPROM.h<span class="pl-pds">&gt;</span></span></td>

                                                                     ^

C:\Program Files (x86)\Arduino\libraries\Otto/Otto.h:644:69: error: stray '#' in program

         <td id="LC8" class="blob-code blob-code-inner js-file-line">#<span class="pl-k">include</span> <span class="pl-s"><span class="pl-pds">&lt;</span>US.h<span class="pl-pds">&gt;</span></span></td>

                                                                     ^

C:\Program Files (x86)\Arduino\libraries\Otto/Otto.h:648:69: error: stray '#' in program

         <td id="LC9" class="blob-code blob-code-inner js-file-line">#<span class="pl-k">include</span> <span class="pl-s"><span class="pl-pds">&lt;</span>LedMatrix.h<span class="pl-pds">&gt;</span></span></td>

                                                                     ^

C:\Program Files (x86)\Arduino\libraries\Otto/Otto.h:652:70: error: stray '#' in program

         <td id="LC10" class="blob-code blob-code-inner js-file-line">#<span class="pl-k">include</span> <span class="pl-s"><span class="pl-pds">&lt;</span>BatReader.h<span class="pl-pds">&gt;</span></span></td>

                                                                      ^

C:\Program Files (x86)\Arduino\libraries\Otto/Otto.h:661:70: error: stray '#' in program

         <td id="LC12" class="blob-code blob-code-inner js-file-line">#<span class="pl-k">include</span> <span class="pl-s"><span class="pl-pds">&quot;</span>Otto_mouths.h<span class="pl-pds">&quot;</span></span></td>

                                                                      ^

C:\Program Files (x86)\Arduino\libraries\Otto/Otto.h:665:70: error: stray '#' in program

         <td id="LC13" class="blob-code blob-code-inner js-file-line">#<span class="pl-k">include</span> <span class="pl-s"><span class="pl-pds">&quot;</span>Otto_sounds.h<span class="pl-pds">&quot;</span></span></td>

                                                                      ^

C:\Program Files (x86)\Arduino\libraries\Otto/Otto.h:669:70: error: stray '#' in program

         <td id="LC14" class="blob-code blob-code-inner js-file-line">#<span class="pl-k">include</span> <span class="pl-s"><span class="pl-pds">&quot;</span>Otto_gestures.h<span class="pl-pds">&quot;</span></span></td>

                                                                      ^

C:\Program Files (x86)\Arduino\libraries\Otto/Otto.h:687:70: error: stray '#' in program

         <td id="LC18" class="blob-code blob-code-inner js-file-line">#<span class="pl-k">define</span> <span class="pl-en">FORWARD</span>     <span class="pl-c1">1</span></td>

                                                                      ^

C:\Program Files (x86)\Arduino\libraries\Otto/Otto.h:691:70: error: stray '#' in program

         <td id="LC19" class="blob-code blob-code-inner js-file-line">#<span class="pl-k">define</span> <span class="pl-en">BACKWARD</span>    -<span class="pl-c1">1</span></td>

                                                                      ^

C:\Program Files (x86)\Arduino\libraries\Otto/Otto.h:695:70: error: stray '#' in program

         <td id="LC20" class="blob-code blob-code-inner js-file-line">#<span class="pl-k">define</span> <span class="pl-en">LEFT</span>        <span class="pl-c1">1</span></td>

                                                                      ^

C:\Program Files (x86)\Arduino\libraries\Otto/Otto.h:699:70: error: stray '#' in program

         <td id="LC21" class="blob-code blob-code-inner js-file-line">#<span class="pl-k">define</span> <span class="pl-en">RIGHT</span>       -<span class="pl-c1">1</span></td>

                                                                      ^

C:\Program Files (x86)\Arduino\libraries\Otto/Otto.h:703:70: error: stray '#' in program

         <td id="LC22" class="blob-code blob-code-inner js-file-line">#<span class="pl-k">define</span> <span class="pl-en">SMALL</span>       <span class="pl-c1">5</span></td>

                                                                      ^

C:\Program Files (x86)\Arduino\libraries\Otto/Otto.h:707:70: error: stray '#' in program

         <td id="LC23" class="blob-code blob-code-inner js-file-line">#<span class="pl-k">define</span> <span class="pl-en">MEDIUM</span>      <span class="pl-c1">15</span></td>

                                                                      ^

C:\Program Files (x86)\Arduino\libraries\Otto/Otto.h:711:70: error: stray '#' in program

         <td id="LC24" class="blob-code blob-code-inner js-file-line">#<span class="pl-k">define</span> <span class="pl-en">BIG</span>         <span class="pl-c1">30</span></td>

                                                                      ^

C:\Program Files (x86)\Arduino\libraries\Otto/Otto.h:720:70: error: stray '#' in program

         <td id="LC26" class="blob-code blob-code-inner js-file-line">#<span class="pl-k">define</span> <span class="pl-en">PIN_Buzzer</span>  <span class="pl-c1">13</span></td>

                                                                      ^

C:\Program Files (x86)\Arduino\libraries\Otto/Otto.h:724:70: error: stray '#' in program

         <td id="LC27" class="blob-code blob-code-inner js-file-line">#<span class="pl-k">define</span> <span class="pl-en">PIN_Trigger</span> <span class="pl-c1">8</span></td>

                                                                      ^
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
EddieMontana, 2018-10-06:
Update! I got them to work by copying the libraries in the C:\Users\Eddie & Tina\Documents\Arduino\libraries. Originally I had all libraries at C:\Program Files (x86)\Arduino\libraries and the codes were not compiling. Now I have them at both locations and the codes are compiling well. I did not try to upload them, but I anticipate they should work.
Obviously I'm new at this... thanks again to the designer of this awesome robot.

Closed 2018-10-06.

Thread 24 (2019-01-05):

Error compiling for board arduino

freekvh, 2019-01-05:
## Explanation of the problem:
I just got my Ottobot, it works well (was missing one screw though for the on/off button, it's also not listed on the part page of the manual by the way. Also, I had to select for the Processor: Atmega328P (old bootloader), that was not mentioned in the manual.)

But I worked around that. I now have the following issue, some programs work, like Smooth criminal and all the "songs". But Otto avoid does not compile, I get the following error:
(By the way I use the Arduino 1.8.8 software)

```

Arduino: 1.8.8 (Windows 10), Board: "Arduino Nano, ATmega328P"

C:\Program Files (x86)\Arduino\arduino-builder -dump-prefs -logger=machine -hardware C:\Program Files (x86)\Arduino\hardware -tools C:\Program Files (x86)\Arduino\tools-builder -tools C:\Program Files (x86)\Arduino\hardware\tools\avr -built-in-libraries C:\Program Files (x86)\Arduino\libraries -libraries C:\Users\nlv24077\Documents\Arduino\libraries -fqbn=arduino:avr:nano:cpu=atmega328 -ide-version=10808 -build-path C:\Users\nlv24077\AppData\Local\Temp\arduino_build_577007 -warnings=none -build-cache C:\Users\nlv24077\AppData\Local\Temp\arduino_cache_726196 -prefs=build.warn_data_percentage=75 -prefs=runtime.tools.avr-gcc.path=C:\Program Files (x86)\Arduino\hardware\tools\avr -prefs=runtime.tools.avr-gcc-5.4.0-atmel3.6.1-arduino2.path=C:\Program Files (x86)\Arduino\hardware\tools\avr -prefs=runtime.tools.avrdude.path=C:\Program Files (x86)\Arduino\hardware\tools\avr -prefs=runtime.tools.avrdude-6.3.0-arduino14.path=C:\Program Files (x86)\Arduino\hardware\tools\avr -prefs=runtime.tools.arduinoOTA.path=C:\Program Files (x86)\Arduino\hardware\tools\avr -prefs=runtime.tools.arduinoOTA-1.2.1.path=C:\Program Files (x86)\Arduino\hardware\tools\avr -verbose C:\Users\nlv24077\Documents\Arduino\Otto_avoid\Otto_avoid.ino
C:\Program Files (x86)\Arduino\arduino-builder -compile -logger=machine -hardware C:\Program Files (x86)\Arduino\hardware -tools C:\Program Files (x86)\Arduino\tools-builder -tools C:\Program Files (x86)\Arduino\hardware\tools\avr -built-in-libraries C:\Program Files (x86)\Arduino\libraries -libraries C:\Users\nlv24077\Documents\Arduino\libraries -fqbn=arduino:avr:nano:cpu=atmega328 -ide-version=10808 -build-path C:\Users\nlv24077\AppData\Local\Temp\arduino_build_577007 -warnings=none -build-cache C:\Users\nlv24077\AppData\Local\Temp\arduino_cache_726196 -prefs=build.warn_data_percentage=75 -prefs=runtime.tools.avr-gcc.path=C:\Program Files (x86)\Arduino\hardware\tools\avr -prefs=runtime.tools.avr-gcc-5.4.0-atmel3.6.1-arduino2.path=C:\Program Files (x86)\Arduino\hardware\tools\avr -prefs=runtime.tools.avrdude.path=C:\Program Files (x86)\Arduino\hardware\tools\avr -prefs=runtime.tools.avrdude-6.3.0-arduino14.path=C:\Program Files (x86)\Arduino\hardware\tools\avr -prefs=runtime.tools.arduinoOTA.path=C:\Program Files (x86)\Arduino\hardware\tools\avr -prefs=runtime.tools.arduinoOTA-1.2.1.path=C:\Program Files (x86)\Arduino\hardware\tools\avr -verbose C:\Users\nlv24077\Documents\Arduino\Otto_avoid\Otto_avoid.ino
Using board 'nano' from platform in folder: C:\Program Files (x86)\Arduino\hardware\arduino\avr
Using core 'arduino' from platform in folder: C:\Program Files (x86)\Arduino\hardware\arduino\avr
Detecting libraries used...
"C:\\Program Files (x86)\\Arduino\\hardware\\tools\\avr/bin/avr-g++" -c -g -Os -w -std=gnu++11 -fpermissive -fno-exceptions -ffunction-sections -fdata-sections -fno-threadsafe-statics -Wno-error=narrowing -flto -w -x c++ -E -CC -mmcu=atmega328p -DF_CPU=16000000L -DARDUINO=10808 -DARDUINO_AVR_NANO -DARDUINO_ARCH_AVR "-IC:\\Program Files (x86)\\Arduino\\hardware\\arduino\\avr\\cores\\arduino" "-IC:\\Program Files (x86)\\Arduino\\hardware\\arduino\\avr\\variants\\eightanaloginputs" "C:\\Users\\nlv24077\\AppData\\Local\\Temp\\arduino_build_577007\\sketch\\Otto_avoid.ino.cpp" -o nul
"C:\\Program Files (x86)\\Arduino\\hardware\\tools\\avr/bin/avr-g++" -c -g -Os -w -std=gnu++11 -fpermissive -fno-exceptions -ffunction-sections -fdata-sections -fno-threadsafe-statics -Wno-error=narrowing -flto -w -x c++ -E -CC -mmcu=atmega328p -DF_CPU=16000000L -DARDUINO=10808 -DARDUINO_AVR_NANO -DARDUINO_ARCH_AVR "-IC:\\Program Files (x86)\\Arduino\\hardware\\arduino\\avr\\cores\\arduino" "-IC:\\Program Files (x86)\\Arduino\\hardware\\arduino\\avr\\variants\\eightanaloginputs" "-IC:\\Program Files (x86)\\Arduino\\libraries\\Servo\\src" "C:\\Users\\nlv24077\\AppData\\Local\\Temp\\arduino_build_577007\\sketch\\Otto_avoid.ino.cpp" -o nul
"C:\\Program Files (x86)\\Arduino\\hardware\\tools\\avr/bin/avr-g++" -c -g -Os -w -std=gnu++11 -fpermissive -fno-exceptions -ffunction-sections -fdata-sections -fno-threadsafe-statics -Wno-error=narrowing -flto -w -x c++ -E -CC -mmcu=atmega328p -DF_CPU=16000000L -DARDUINO=10808 -DARDUINO_AVR_NANO -DARDUINO_ARCH_AVR "-IC:\\Program Files (x86)\\Arduino\\hardware\\arduino\\avr\\cores\\arduino" "-IC:\\Program Files (x86)\\Arduino\\hardware\\arduino\\avr\\variants\\eightanaloginputs" "-IC:\\Program Files (x86)\\Arduino\\libraries\\Servo\\src" "-IC:\\Users\\nlv24077\\Documents\\Arduino\\libraries\\Oscillator" "C:\\Users\\nlv24077\\AppData\\Local\\Temp\\arduino_build_577007\\sketch\\Otto_avoid.ino.cpp" -o nul
"C:\\Program Files (x86)\\Arduino\\hardware\\tools\\avr/bin/avr-g++" -c -g -Os -w -std=gnu++11 -fpermissive -fno-exceptions -ffunction-sections -fdata-sections -fno-threadsafe-statics -Wno-error=narrowing -flto -w -x c++ -E -CC -mmcu=atmega328p -DF_CPU=16000000L -DARDUINO=10808 -DARDUINO_AVR_NANO -DARDUINO_ARCH_AVR "-IC:\\Program Files (x86)\\Arduino\\hardware\\arduino\\avr\\cores\\arduino" "-IC:\\Program Files (x86)\\Arduino\\hardware\\arduino\\avr\\variants\\eightanaloginputs" "-IC:\\Program Files (x86)\\Arduino\\libraries\\Servo\\src" "-IC:\\Users\\nlv24077\\Documents\\Arduino\\libraries\\Oscillator" "-IC:\\Users\\nlv24077\\Documents\\Arduino\\libraries\\US" "C:\\Users\\nlv24077\\AppData\\Local\\Temp\\arduino_build_577007\\sketch\\Otto_avoid.ino.cpp" -o nul
"C:\\Program Files (x86)\\Arduino\\hardware\\tools\\avr/bin/avr-g++" -c -g -Os -w -std=gnu++11 -fpermissive -fno-exceptions -ffunction-sections -fdata-sections -fno-threadsafe-statics -Wno-error=narrowing -flto -w -x c++ -E -CC -mmcu=atmega328p -DF_CPU=16000000L -DARDUINO=10808 -DARDUINO_AVR_NANO -DARDUINO_ARCH_AVR "-IC:\\Program Files (x86)\\Arduino\\hardware\\arduino\\avr\\cores\\arduino" "-IC:\\Program Files (x86)\\Arduino\\hardware\\arduino\\avr\\variants\\eightanaloginputs" "-IC:\\Program Files (x86)\\Arduino\\libraries\\Servo\\src" "-IC:\\Users\\nlv24077\\Documents\\Arduino\\libraries\\Oscillator" "-IC:\\Users\\nlv24077\\Documents\\Arduino\\libraries\\US" "-IC:\\Users\\nlv24077\\Documents\\Arduino\\libraries\\Otto" "C:\\Users\\nlv24077\\AppData\\Local\\Temp\\arduino_build_577007\\sketch\\Otto_avoid.ino.cpp" -o nul
"C:\\Program Files (x86)\\Arduino\\hardware\\tools\\avr/bin/avr-g++" -c -g -Os -w -std=gnu++11 -fpermissive -fno-exceptions -ffunction-sections -fdata-sections -fno-threadsafe-statics -Wno-error=narrowing -flto -w -x c++ -E -CC -mmcu=atmega328p -DF_CPU=16000000L -DARDUINO=10808 -DARDUINO_AVR_NANO -DARDUINO_ARCH_AVR "-IC:\\Program Files (x86)\\Arduino\\hardware\\arduino\\avr\\cores\\arduino" "-IC:\\Program Files (x86)\\Arduino\\hardware\\arduino\\avr\\variants\\eightanaloginputs" "-IC:\\Program Files (x86)\\Arduino\\libraries\\Servo\\src" "-IC:\\Users\\nlv24077\\Documents\\Arduino\\libraries\\Oscillator" "-IC:\\Users\\nlv24077\\Documents\\Arduino\\libraries\\US" "-IC:\\Users\\nlv24077\\Documents\\Arduino\\libraries\\Otto" "-IC:\\Program Files (x86)\\Arduino\\hardware\\arduino\\avr\\libraries\\EEPROM\\src" "C:\\Users\\nlv24077\\AppData\\Local\\Temp\\arduino_build_577007\\sketch\\Otto_avoid.ino.cpp" -o nul
"C:\\Program Files (x86)\\Arduino\\hardware\\tools\\avr/bin/avr-g++" -c -g -Os -w -std=gnu++11 -fpermissive -fno-exceptions -ffunction-sections -fdata-sections -fno-threadsafe-statics -Wno-error=narrowing -flto -w -x c++ -E -CC -mmcu=atmega328p -DF_CPU=16000000L -DARDUINO=10808 -DARDUINO_AVR_NANO -DARDUINO_ARCH_AVR "-IC:\\Program Files (x86)\\Arduino\\hardware\\arduino\\avr\\cores\\arduino" "-IC:\\Program Files (x86)\\Arduino\\hardware\\arduino\\avr\\variants\\eightanaloginputs" "-IC:\\Program Files (x86)\\Arduino\\libraries\\Servo\\src" "-IC:\\Users\\nlv24077\\Documents\\Arduino\\libraries\\Oscillator" "-IC:\\Users\\nlv24077\\Documents\\Arduino\\libraries\\US" "-IC:\\Users\\nlv24077\\Documents\\Arduino\\libraries\\Otto" "-IC:\\Program Files (x86)\\Arduino\\hardware\\arduino\\avr\\libraries\\EEPROM\\src" "-IC:\\Users\\nlv24077\\Documents\\Arduino\\libraries\\BatReader" "C:\\Users\\nlv24077\\AppData\\Local\\Temp\\arduino_build_577007\\sketch\\Otto_avoid.ino.cpp" -o nul
"C:\\Program Files (x86)\\Arduino\\hardware\\tools\\avr/bin/avr-g++" -c -g -Os -w -std=gnu++11 -fpermissive -fno-exceptions -ffunction-sections -fdata-sections -fno-threadsafe-statics -Wno-error=narrowing -flto -w -x c++ -E -CC -mmcu=atmega328p -DF_CPU=16000000L -DARDUINO=10808 -DARDUINO_AVR_NANO -DARDUINO_ARCH_AVR "-IC:\\Program Files (x86)\\Arduino\\hardware\\arduino\\avr\\cores\\arduino" "-IC:\\Program Files (x86)\\Arduino\\hardware\\arduino\\avr\\variants\\eightanaloginputs" "-IC:\\Program Files (x86)\\Arduino\\libraries\\Servo\\src" "-IC:\\Users\\nlv24077\\Documents\\Arduino\\libraries\\Oscillator" "-IC:\\Users\\nlv24077\\Documents\\Arduino\\libraries\\US" "-IC:\\Users\\nlv24077\\Documents\\Arduino\\libraries\\Otto" "-IC:\\Program Files (x86)\\Arduino\\hardware\\arduino\\avr\\libraries\\EEPROM\\src" "-IC:\\Users\\nlv24077\\Documents\\Arduino\\libraries\\BatReader" "C:\\Program Files (x86)\\Arduino\\libraries\\Servo\\src\\avr\\Servo.cpp" -o nul
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
letoangiakhanhg, 2019-03-03:
i have the same problem at my nano, what is your new code, pls help me

GalUnDrux, 2019-03-10:
I get the same error, even with the "updated" code.. which just replaces oscilator.h not Otto.h and Otto.cpp which contain the problem..
the problem seems to be with the LedMatrix entry within Otto.h.
No matter what i try i can not get any code to work with my laser cut v2 Otto Basic...
any help would be greatly apreciated!

GalUnDrux, 2019-03-10:
found a solution:
take the Otto folder from the App directory of the Otto-Plus Zip file from GitHub:
Otto-Plus\PLUS-master\APP\Libraries
copy all libraries to program files/Arduino/libraries (or your Arduino install directory)
it seems to have MaxMatrix rather than LEDMatrix inside the Otto.h... replacing the other Otto library directory seems to solve the compiling issue for Nano..

ProgrammerBruce, 2019-05-20:
Using Arduino IDE 1.8.9, without any changes, with the libraries copied from this repository to Documents/Arduino/libraries, I just confirmed that all of the .ino sketches compile successfully.  This includes:
Otto_allmoves
Otto_avoid_mhs
Otto_avoid_TRIMS
Otto_easycal
Otto_Footalign
Otto_happybirthday
Otto_jingle
Otto_MarioBros
Otto_Mblock_ScratchMode_Serial
Otto_push
Otto_run
Otto_singleladies
Otto_smooth_criminal
Otto_smooth_criminal_US

(Otto_ESP32 is a different issue.)

There may be an issue with differences between the .zip files and the other files in the libraries directory.  (The .zip files should probably be deleted from this repository, but that's a different issue.)

So, this issue #24 about a compiling problem should be closed.

cparrapa, 2019-05-20:
thanks @ProgrammerBruce for confirming that the codes work with no problems anymore

Closed 2019-05-20.

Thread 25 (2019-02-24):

Fit for symmetric foot unclear - detailed picture or graphic available?

justinotherguy, 2019-02-24:
Hello there,

after printing the 3d files for OTTO it's unclear to me how the foot and the leg are supposed to fit together. Keeping to the diagrams in OttoDIY_InstructionsManual_V09.PDF on page 4 I end up with a leg that fits very loosely in the new leg (both are OttoDIY+_[foot|leg]_v08.stl).

Up until v5 the feet very asymmetrical with holes which very used to tightly mount the servo.
While I greatly appreciate the fact that the two feet are identical now, it seems I fail to understand how this is supposed to become stable.

Would you have any pictures that show details for an assembled foot + leg combination in v7 oder v8?

As I'm not suggesting an improvement but merely ask a question, let me know whether this (or thingiverse) is the right place.

Thanks guys :)

cparrapa, 2019-03-26:
Hi Justin
i will personally make a video to show this update the new feet design might not be the perfect fit specially for SG90 servos but allows to easily use any foot avoiding confusions, it seems that in some printers is ”quite loose“ so some already created an additional adapter to reinforce that will keep the compatibility with MG90 servos

thanks!

justinotherguy, 2019-03-28:
Hi @cparrapa ,
thx, great!
Maybe you can give the dimensions of the foot and the leg (the way they should be and do fit). So I can check whether it's my printer that  is so far off.
Thanks :)
Regards, J.

cparrapa, 2019-03-28:
Hi Justin
Have a look to the 3D model here https://gallery.autodesk.com/fusion360/projects/otto-diyplus
you can measure any part and distance, please check and let me know. Sometimes is the very tricky tolerances to make a perfect fit
You are welcome

Closed 2019-05-20.

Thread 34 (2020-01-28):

Negative offset used for walking, but oscillator.h uses uint

Tobiassss, 2020-01-28:
My newly build OTTO couldn't walk, because it's right foot was not moving. It was just held in a fixed, angled position. Its right foot and all other servos worked (moved) correctly. By homing, all servos were correctly set into default position.

After some debugging, I could localize the problem: Oscillator::refresh calculated false huge numbers for the right foot servo, because the used offset (_O) was huge. It should be -4. The same with other negative values. Positives worked fine.
Digging deeper I found that  Oscillator.h only handles positive values:
`void SetO(unsigned int O) {_O=O;};`

By changing it to signed int, it works for me:
`void SetO(signed int O) {_O=O;};`

Did I miss something and my misbehaving OTTO has some other problems, or is this really an issue?

cparrapa, 2020-01-28:
Hi Tobias
Are you using ESP32 or ESP8266 board?

Tobiassss, 2020-01-29:
ESP32
TTGO T-Display (https://github.com/Xinyuan-LilyGO/TTGO-T-Display)

Closed 2022-02-10.

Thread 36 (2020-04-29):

Specified folder/zip files does not contain a valid library

Bmac947, 2020-04-29:
I'm getting this error when trying to use the Examples folder.

carl1961, 2020-04-29:
did you copy the Libraries folder to the ardunio libraries folder?    C:\Users\Carl\Documents\Arduino\libraries
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

Bmac947, 2020-04-29:
Thanks for the email! I have copied most of them after deleting and starting again,. The main issue in the Examples folder throwing the error!

[cid:9E77FDC3-7394-4833-9C93-A03A88ACE616@gateway]

On 29 Apr 2020, at 1:01 pm, carl1961 <notifications@github.com<mailto:notifications@github.com>> wrote:

did you copy the Libraries folder to the ardunio libraries folder? C:\Users\Carl\Documents\Arduino\libraries
[esp lib]<https://user-images.githubusercontent.com/3056821/80557213-c8cc7480-899b-11ea-9d31-4a308d1d9c42.png>

—
You are receiving this because you authored the thread.
Reply to this email directly, view it on GitHub<https://github.com/OttoDIY/ESP/issues/36#issuecomment-620964851>, or unsubscribe<https://github.com/notifications/unsubscribe-auth/AODJDDKXDXMO6SAV7MN4I23RO6KAXANCNFSM4MTKH45Q>.

Ben McKenzie
Design Technology Coordinator
P:+61 3 5560 0888 | E: bmckenzie@emmanuel.vic.edu.au<mailto:bmckenzie@emmanuel.vic.edu.au>
________________________________

[cid:image3c4a64.PNG@2aebdcf1.45b387db]
Emmanuel College

McAuley Campus

37 Ardlie St

Warrnambool, Victoria 3280      Rice Campus
42 Canterbury Rd
Warrnambool, Victoria 3280

www.emmanuel.vic.edu.au<http://www.emmanuel.vic.edu.au>
Warrnambool: Australia’s Most Liveable City<http://www.warrnambool.com/>

[cid:image2e51e8.JPG@41ad6a6c.4b8af60d]<https://www.emmanuel.vic.edu.au>
________________________________
The information transmitted, including attachments, is intended only for the person(s) or entity to which it is addressed and may
contain confidential and/or privileged material. Any review, retransmission, dissemination or other use of, or taking of any action in
reliance upon this information by persons or entities other than the intended recipient is prohibited. If you received this in error
please contact the sender and destroy any copies of this information.

Closed 2021-04-20.

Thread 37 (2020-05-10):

Wrong data type for "O" in oscillator.h

TokenTotem, 2020-05-10:
At line 30 and 50 in oscillator.h, variable "O" is defined as a 'unsigned int' instead of 'int'.
"O" have negative value such as when Otto walk (Otto9.cpp line 282).
There is no apparent impact on Arduino/Atmega but math results are out of wack on ESP32.

Solution: Change data type from "unsigned int" to "int" for variable "O" and "A" at lines 29,30,49,50 in oscillator.h

cparrapa, 2021-04-20:
Hi @TokenTotem
Thanks now we have a separated oscillator library for ESP

Closed 2022-01-30.

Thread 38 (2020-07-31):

Single Code Set: Merge OttoDIYESP & OttoDIYLib

sfranzyshen, 2020-07-31:
after looking at the differences between these two code sets ... it seems they could be merged into one. Is there interest in doing so? or should we continue developing for both?

cparrapa, 2020-07-31:
It seems they are not compatible, we would have to first organize the naming, variables that use same command etc and compile- test them together, give a try and you will see, maybe you can help me to figure out how to make them compatible.

Only after we make sure it works with all Otto we can do a merge

sfranzyshen, 2020-07-31:
I will go ahead and take a shot at unifying them and see exactly where the conflicts are ...

cparrapa, 2020-07-31:
Goo idea thanks

On Friday, July 31, 2020, Scotty Franzyshen <notifications@github.com>
wrote:

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

--
Best Regards
----------------------------------------------------------------------
Camilo Parra Palacio / Product Design Engineer
<https://www.behance.net/cparrapa>/ ottodiy.com

sfranzyshen, 2020-09-22:
work has started for[ refactoring of the OttoDIY Robot API (Otto9.h) code to be non-blocking and universally cross-platform for all Arduino environments](https://github.com/sfranzyshen/OttoDIYArduino) ... so far the servo and motion functions have begun ...

sfranzyshen, 2020-09-27:
### we now have added the humanoid support 😄

Refactoring of the OttoDIY Robot API (Otto9.h & Otto9Humanoid.h) code to be universally cross-platform (all-in-one) and 100% backwards compatible for all Arduino environments (Including but not limited to the Arduino Nano, UNO, Nano 33 IOT, Esp8266, and ESP32)

cparrapa, 2020-09-27:
Wow this is amazing how do you suggest we should merge this?

sfranzyshen, 2020-09-27:
> Wow this is amazing how do you suggest we should merge this in the repos?

ultimately, I could see replacing OttoDIYLIB & OttoDIYESP with OttoDIYArduino ...

cparrapa, 2020-09-28:
Hi @sfranzyshen
Yes I think it can just merge all into the main OttoDIYLIB since many documentations have link connected to that and people always go there to download the libraries in that  repo and then we can get rid of the ESP one.

Later i would have to update for Otto Blockly

Then i think we should try to put it in the Arduino library manager so that is easy for people to install them and stay updated like any other arduino library https://github.com/arduino/Arduino/wiki/Library-Manager-FAQ

thanks

Closed 2021-04-20.

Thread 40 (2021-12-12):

Add support for ESP32devC board

samuk, 2021-12-12:
# Issue Template

## Explain the problem:

*Is it a code issue? - make sure you are using the right libraries and Mblock or Arduino software, please post a screenshot.

In the Otto blockly interface I cannot add ESP32devC as a supported board.

Specifically, I would like to use this open hardware version:  [ESP32-WROVER-DevKit-Lipo](https://www.olimex.com/Products/IoT/ESP32/ESP32-DevKit-LiPo/open-source-hardware) but I believe it is pin-compatible with all ESP32devC boards.

As an aside, I wonder if some kind of HAL system would be possible as used [here](https://github.com/cyberman54/ESP32-Paxcounter/tree/master/src/hal)

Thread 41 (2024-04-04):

Use more powerful micro controller

mohiuya009, 2024-04-04:
Please add support / code for esp32 (and pico) so we can have more rom (4mb) and built in wifi Bluetooth.

sfranzyshen, 2024-05-05:
There are plans to add OttoNinja back into the OttoDIYLib & add full support for avr, esp, and pico with both native and external module bluetooth support. No timeline as of yet.

https://github.com/OttoDIY/OttoDIYLib/tree/devel

Closed 2024-05-05.

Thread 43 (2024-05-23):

Not an issue, just telling

jaiwiwjwjwisn, 2024-05-23:
Why not use esp32 as microcontroller? It has more ram, 4MB flash memory and built in wifi Bluetooth... That will be great.

jaiwiwjwjwisn, 2024-05-23:
Maybe we will also be able to ota update.

jaiwiwjwjwisn, 2024-05-23:
I found one but that's only shield and very outdated

cparrapa, 2024-05-28:
We never found a proper servo library for esp32 they all act very strange, any recommendation @jaiwiwjwjwisn ?

guavuavcycayfayqvqu, 2024-06-01:
> We never found a proper servo library for esp32 they all act very strange, any recommendation @jaiwiwjwjwisn ?

Please send repo /link I'm gonna check out.

guavuavcycayfayqvqu, 2024-06-01:
It's very painful to see a great project like otto can't use powerful microcontroller because of servo library.

guavuavcycayfayqvqu, 2024-06-01:
> We never found a proper servo library for esp32 they all act very strange, any recommendation @jaiwiwjwjwisn ?

Bytheway  rpi pico is also powerful and has 2MB flash (16MB in clones) and almost same size as arduino nano.  Best part is it has a good servo Library, please checkout.  And  unleash true potential of otto 🥰.

guavuavcycayfayqvqu, 2024-06-01:
Any thoughts @cparrapa ? https://github.com/guavuavcycayfayqvqu/OttoNinja/tree/devel/servo

sfranzyshen, 2024-06-02:
Hi @guavuavcycayfayqvqu or jaiwiwjwjwisn

We would like to help you. Please see the information in the OttoDIYLib comment https://github.com/OttoDIY/OttoDIYLib/issues/70

cparrapa, 2024-06-06:
It is a pity indeed @guavuavcycayfayqvqu but once you test them in the hardware you will see what I meant, @sfranzyshen  is doing a good work to have the compatibility and performance qual for nano and ESP boards.

There are many:
https://madhephaestus.github.io/ESP32Servo/annotated.html
https://github.com/jkb-git/ESP32Servo
https://github.com/RoboticsBrno/ServoESP32 we were also testing and it was giving some errors and abrupt movements

They need to be properly merged with the Otto DIY Lib in a ways that it keeps backwards compatibility.

I also forgot to mention hardware was limitation until the new https://hprobots.com/ kit came out that one is ESP32 based and has the perfect size for Otto.

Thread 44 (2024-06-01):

Add support for esp32

guavuavcycayfayqvqu, 2024-06-01:
I really want to build otto ninja with esp32 that's fast and have 16MB flash(s3 ) and wifi for app control. But i couldn't find any tutorial for esp32. Is it possible? (I'm absolute noob). And can it fit inside otto ninja 3d printed parts?

sfranzyshen, 2024-06-02:
Hi @guavuavcycayfayqvqu

Please see my response to your issue over at the OttoDIYLib repo https://github.com/OttoDIY/OttoDIYLib/issues/70

guavuavcycayfayqvqu, 2024-06-02:
> Hi @guavuavcycayfayqvqu
>
> Please see my response to your issue over at the OttoDIYLib repo [OttoDIY/OttoDIYLib#70](https://github.com/OttoDIY/OttoDIYLib/issues/70)

Yes thanks

Closed 2024-06-06.

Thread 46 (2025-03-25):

HC-SR04  not work

qulet, 2025-03-25:
I made a robot otto ninja APP code on esp 2866 LOLIN board (Wemos) D1 mini clone.
What is the actual function of the HC-SR04 sensor? .
I have it connected to D1-Trig and D2 Echo and power supply +5V and GND. I do not see any reaction to the obstacle during the robot's movement. It also does not respond to hand gestures.

qulet, 2025-03-25:
My second question. How do I programmatically adjust the 360   foot servo so that it is motionless in a non-moving position. In my case, LF has rotation and RF is motionless. I am talking about the robot's standing position.

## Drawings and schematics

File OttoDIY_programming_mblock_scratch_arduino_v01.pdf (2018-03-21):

# CODING GUIDE

### mblock

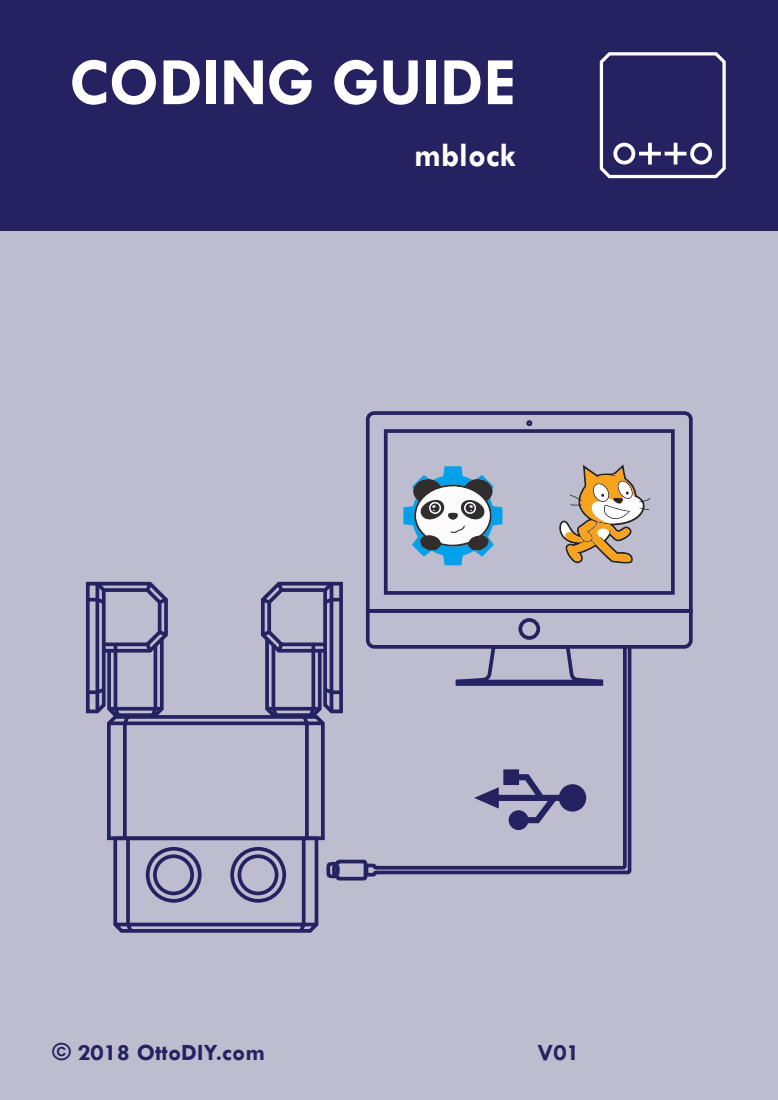
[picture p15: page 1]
© 2018 OttoDIY.com

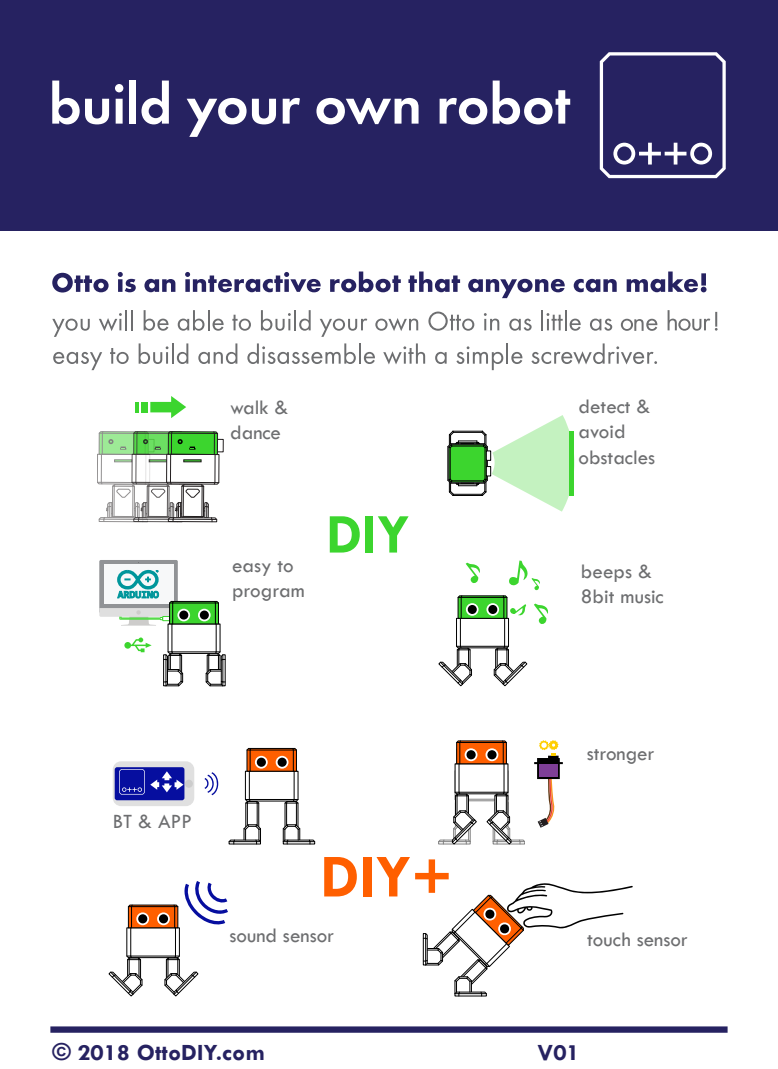
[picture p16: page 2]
beeps & 8bit music; detect & avoid obstacles; walk & dance; easy to program; BT & APP; sound sensor; touch sensor; stronger; © 2018 OttoDIY.com

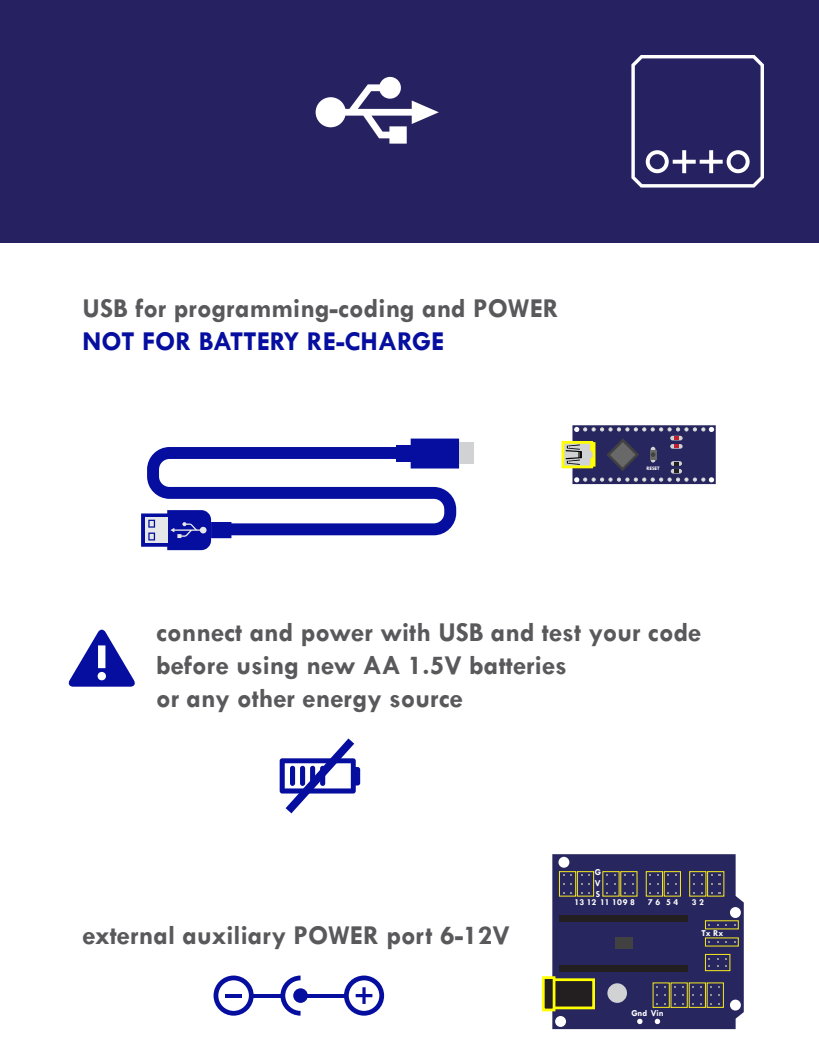
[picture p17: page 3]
RESET; Gnd Vin

USB for programming-coding and POWER
NOT FOR BATTERY RE-CHARGE

connect and power with USB and test your code
before using new AA 1.5V batteries
or any other energy source

external auxiliary POWER port 6-12V

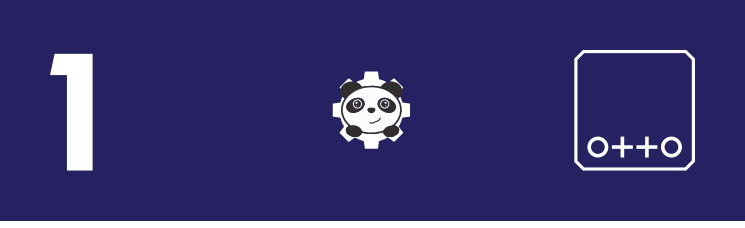
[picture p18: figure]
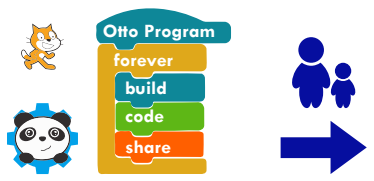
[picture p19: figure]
forever; Otto Program; share; code; build

download Arduino for FREE to your computer
from http://www.mblock.cc/software/mblock/mblock3/ mblock is a graphical programming environment based on Scratch 2.0 Open Source Code that makes it easy to program electronics projects and create interactive robots like Otto; with the Arduino mode you can view both the Arduino source changes in real-time and the graphical blocks corresponding to the C language code, so that you can process a smooth transition to advanced programming.

choose the appropriate Operating System installation package for your computer.

a

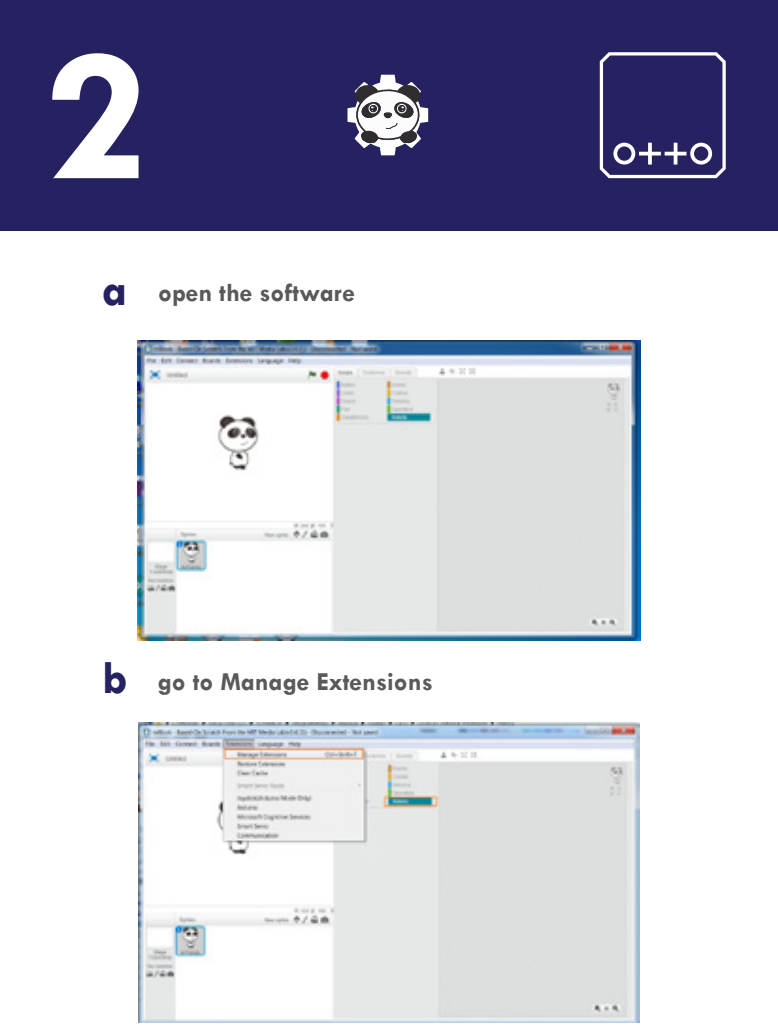
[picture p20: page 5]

open the software

go to Manage Extensions

a

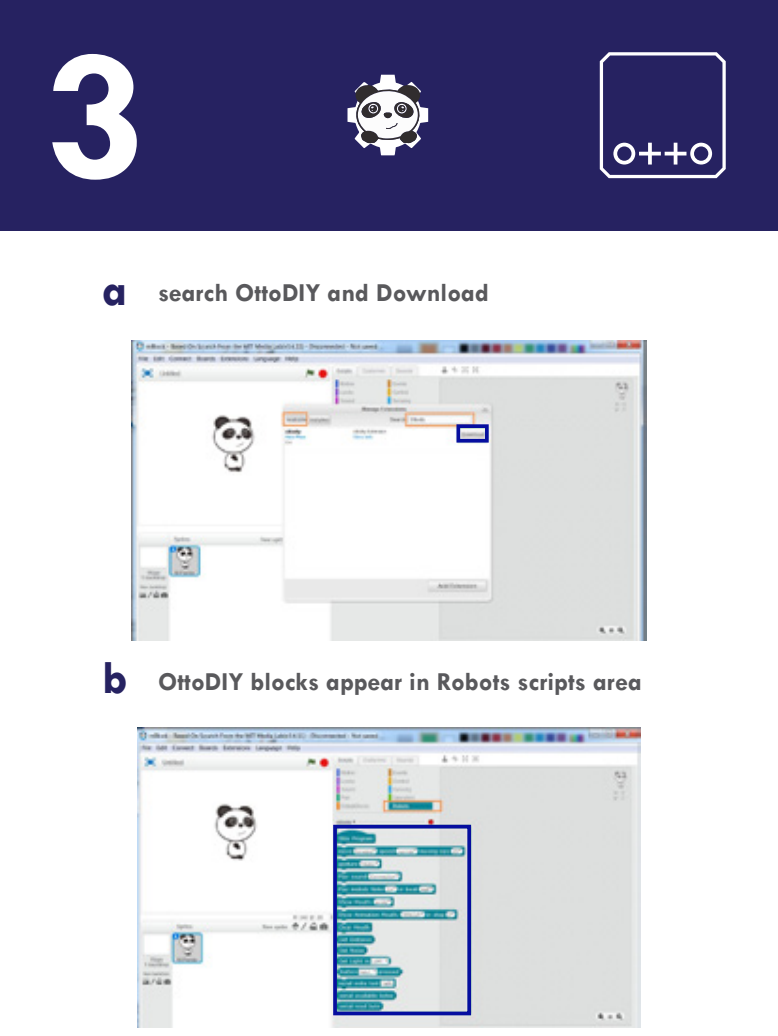
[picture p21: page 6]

search OttoDIY and Download

OttoDIY blocks appear in Robots scripts area

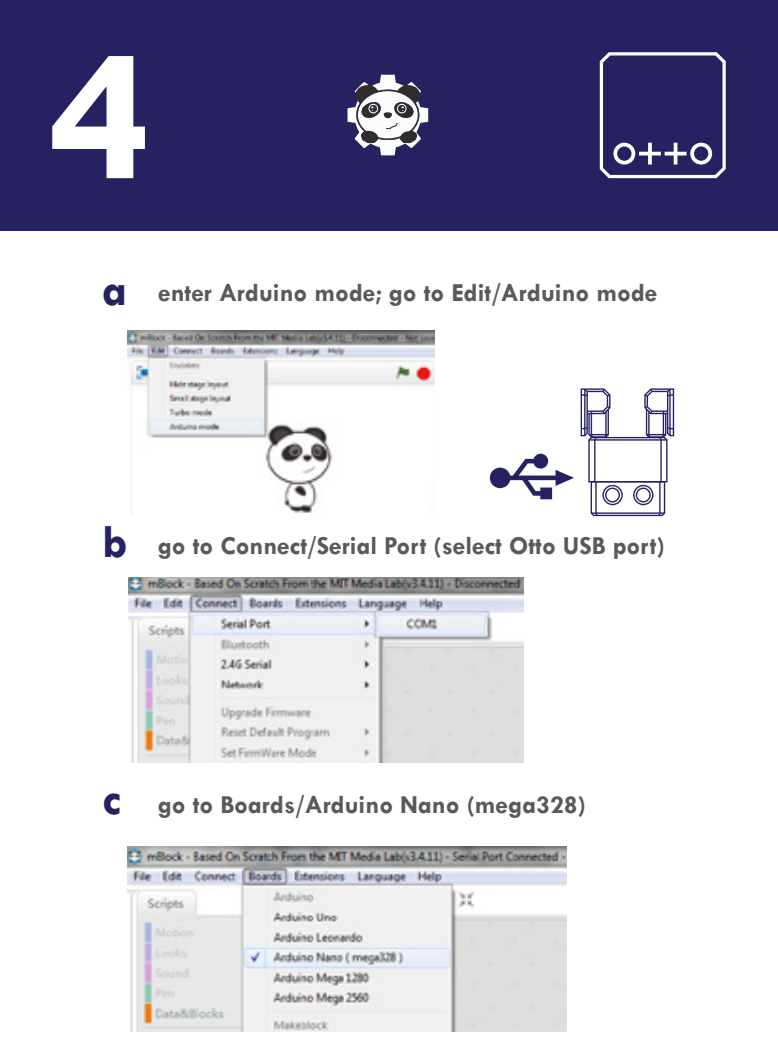
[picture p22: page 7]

a enter Arduino mode; go to Edit/Arduino mode

go to Connect/Serial Port (select Otto USB port)

go to Boards/Arduino Nano (mega328)

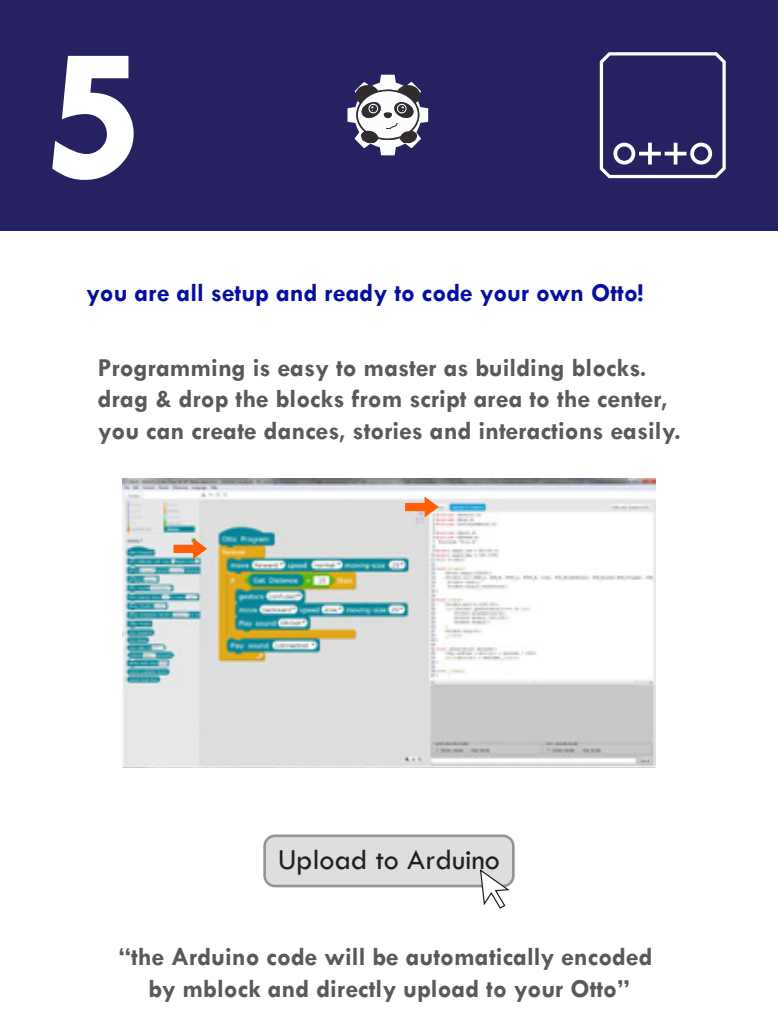
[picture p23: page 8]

you are all setup and ready to code your own Otto!

Programming is easy to master as building blocks.
drag & drop the blocks from script area to the center,
you can create dances, stories and interactions easily.

Upload to Arduino

“the Arduino code will be automatically encoded
by mblock and directly upload to your Otto”

# SIGN UP in ottodiy.com

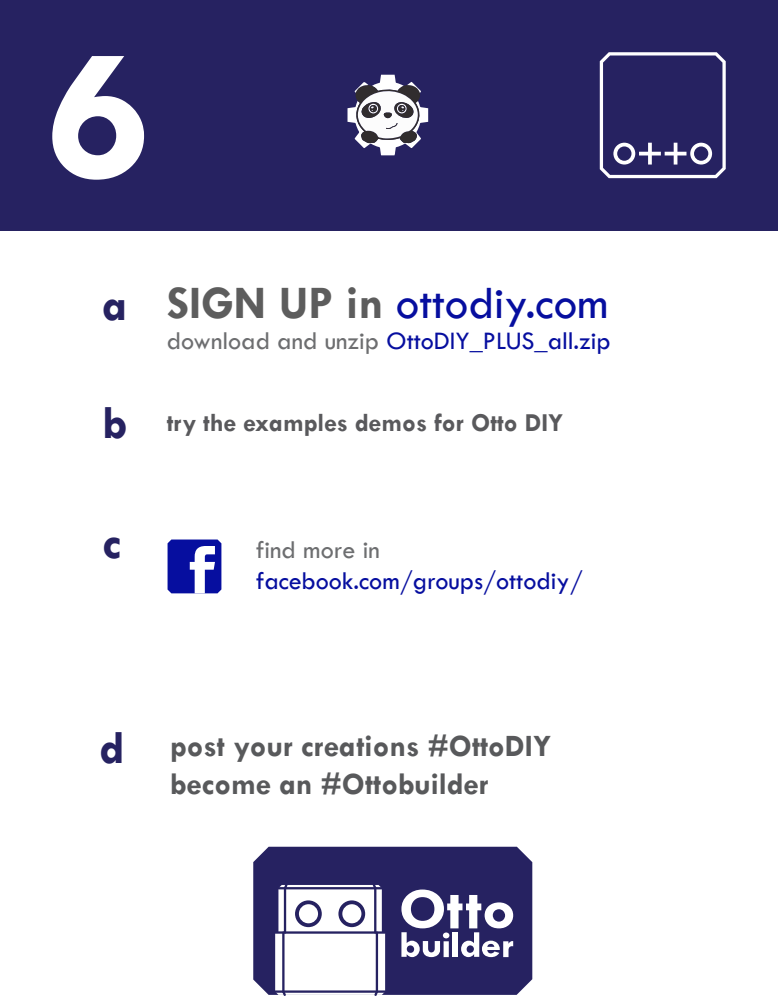
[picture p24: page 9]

download and unzip OttoDIY_PLUS_all.zip
try the examples demos for Otto DIY

find more in
facebook.com/groups/ottodiy/

d post your creations #OttoDIY
become an #Ottobuilder

# CODING GUIDE

### arduino

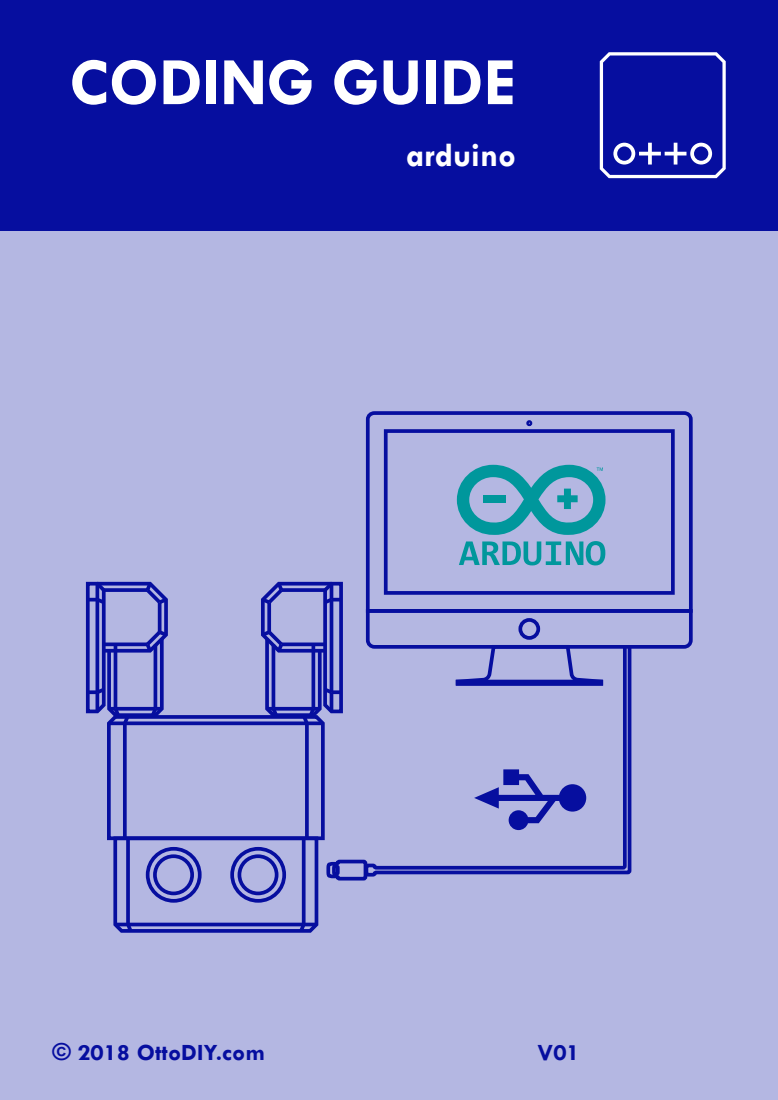
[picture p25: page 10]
© 2018 OttoDIY.com

a

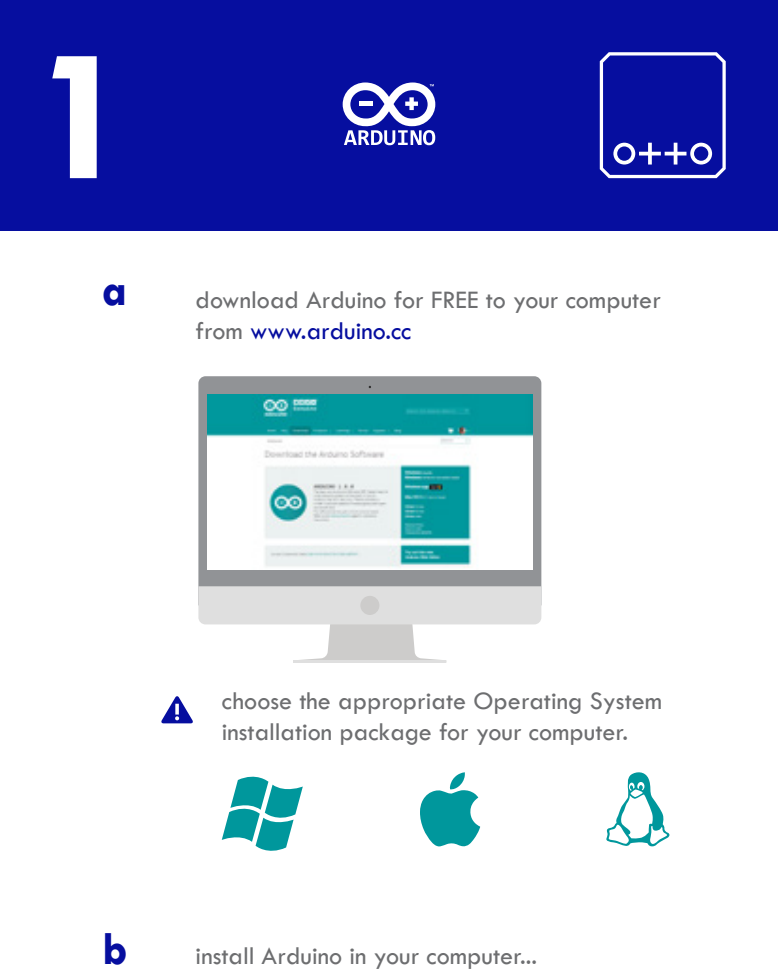
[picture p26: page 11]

download Arduino for FREE to your computer
from www.arduino.cc

choose the appropriate Operating System
installation package for your computer.

install Arduino in your computer...

# SIGN UP in ottodiy.com


download and unzip OttoDIY_PLUS_all.zip

from the “driver” folder install CH341SER
choose the appropriate Operating System
installation package for your computer.
copy or move all “libraries” folders to:

C:\Documents\Arduino\libraries\
(your Arduino library folder location)

copy or move all “Otto_” folders to:

C:\Documents\Arduino\

a


open Arduino and
open Otto_avoid.ino

Connect Otto to your computer USB


select in Arduino Tools/

Board: “Arduino Nano”
Processor: “ATmega328”
Port COM# (where your Otto is connected)

a


verify the code

upload the code

Otto will walk endless until detect
obstacles to avoid

void loop() { if(obstacleDetected){ Otto.sing(S_surprise); Otto.playGesture(OttoFretful); Otto.sing(S_fart3); Otto.walk(2,1300,-1); Otto.turn(2,1000,-1); delay(50); obstacleDetector(); } else{ Otto.walk(1,1000,1); obstacleDetector();; Otto_avoid.ino

in Arduino the principal loop code looks like this:

(S_surprise);; (S_OhOoh);; (S_OhOoh2);; (S_cuddly);; (S_sleeping);; (S_happy);; (S_superHappy);; (S_happy_short);; (S_sad);; (S_confused);; (S_fart1);; (S_fart2);; (S_fart3);; (S_mode1);; (S_mode2);; (S_mode3);; (S_connection);; (S_disconnection);; (S_buttonPushed);; sing function: Otto.sing(S_surprise);; sing function; (“sound to make”)

try change sound:

(OttoSuperHappy);; (OttoSad);; (OttoSleeping);; (OttoFart);; (OttoConfused);; (OttoFretful);; (OttoLove);; (OttoAngry);; (OttoMagic);; (OttoWave);; (OttoVictory);; (OttoFail);; play Gesture function; (“emotion to express”)

play Gesture function:
Otto.playGesture(OttoFretful);

try change emotion:

move functions: Otto.walk(2,1300,-1);; Otto.walk(1,1000,1);; Otto.walk(1,1000,-1);; Otto.turn(3,1000,1);; Otto.turn(3,1000,-1);; Otto.bend(2,1000,1);; Otto.bend(2,500,-1);; Otto.shakeLeg(1,1000,1);; Otto.shakeLeg(1,500,-1);; Otto.jump(1,1000);

move function (“#steps, Time[ms], direction”)

try change move function to:
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

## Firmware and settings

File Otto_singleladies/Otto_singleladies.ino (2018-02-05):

//----------------------------------------------------------------
//-- Otto Dance single ladies by Beyonce
//-- Released under a GPL licencse (http://ottodiy.com)
//-- Author: brico3d.blogspot.com
//-----------------------------------------------------------------
#include <Servo.h>
#include <Oscillator.h>
#include <EEPROM.h>

#define N_SERVOS 4
#define EEPROM_TRIM false //Activate for calibration

#define TRIM_RR 18
#define TRIM_RL 18
#define TRIM_YR 26
#define TRIM_YL 18

#define PIN_RR 3
#define PIN_RL 2
#define PIN_YR 4
#define PIN_YL 5

#define INTERVALTIME 10.0 

Oscillator servo[N_SERVOS];

void drunk (int tempo);
void kickLeft(int tempo);
void kickRight(int tempo);
void pasitos(int steps, int tempo);
void run(int steps, int T=500);
void walk(int steps, int T=1000);
void backyard(int steps, int T=3000);
void moonWalkLeft(int steps, int T=1000);
void moonWalkRight(int steps, int T=1000);
void crusaito(int steps, int T=1000);
void swing(int steps, int T=1000);
void upDown(int steps, int tempo);
void flapping(int steps, int T=1000);

void setup()
{
  Serial.begin(19200);
  
  servo[0].attach(PIN_RR);
  servo[1].attach(PIN_RL);
  servo[2].attach(PIN_YR);
  servo[3].attach(PIN_YL);
  
  int trim;
  
  if(EEPROM_TRIM){
    for(int x=0;x<4;x++){
      trim=EEPROM.read(x);
      if(trim>128)trim=trim-256;
      Serial.print("TRIM ");
      Serial.print(x);
      Serial.print(" en ");
      Serial.println(trim);
      servo[x].SetTrim(trim);
    }
  }
  else{
    servo[0].SetTrim(TRIM_RR);
    servo[1].SetTrim(TRIM_RL);
    servo[2].SetTrim(TRIM_YR);
    servo[3].SetTrim(TRIM_YL);
  }
  
  for(int i=0;i<4;i++) servo[i].SetPosition(90);

}

// TEMPO: 97 BPM
int t=620;
double pause=0;

void loop() {
  
  pasitos(8,t*2);
  crusaito(1,t);
  patada(t);
  delay(t);
  twist(2,t);
  twist(3,t/2);
  upDown(1,t*2);
  patada(t*2);
  drunk(t*2);
  flapping(1,t*2);
  walk(2,t);
  walk(1,t*2);
  backyard(2,t);
  patada(t*2);
  flapping(1,t*2);
  patada(t*2);
  twist(8,t/2);
  moonWalkLeft(2,t);
  crusaito(1,t*2);
  
  for(int i=0; i<2 ;i++){
    lateral_fuerte(0,t);
    lateral_fuerte(1,t);
    upDown(1,t*2);
  }
  
  saludo(1,t*2);
  saludo(1,t);
  delay(t);
  swing(3,t);
  for(int i=0;i<4;i++) servo[i].SetPosition(90);
  delay(t);
  
  lateral_fuerte(0,t);
  lateral_fuerte(1,t);
  lateral_fuerte(0,t/2);
  lateral_fuerte(1,t/2);
  lateral_fuerte(0,t/2);
  delay(t/2);
  lateral_fuerte(0,t);
  lateral_fuerte(1,t);
  lateral_fuerte(0,t/2);
  lateral_fuerte(1,t/2);
  delay(t);
  
  pasitos(1,t*2);
  pasitos(1,t);
  delay(t/2);
  pasitos(1,t*2);
  pasitos(1,t);
  delay(t/2);
     
  crusaito(2,t);
  crusaito(1,t*2);
  crusaito(2,t);
  crusaito(1,t*2);
  crusaito(2,t);
  crusaito(1,t*2);
  
  upDown(2,t);
  crusaito(1,t*2);
  for(int i=0;i<4;i++) servo[i].SetPosition(90);
  delay(t/2);
  pasitos(2,t*2);
  pasitos(2,t);
  flapping(1,t*2);
  upDown(2,t);
  upDown(1,t*2);
  
  for (int i=0; i<4; i++){
    pasitos(1,t);
    delay(t);
  }
  reverencia1(1,t*4);
  reverencia2(1,t*4);
  upDown(1,t);
  run(2,t/2);
  patada(t*2);

  lateral_fuerte(0,t);
  lateral_fuerte(1,t);
  upDown(2,t);
  lateral_fuerte(0,t);
  lateral_fuerte(1,t);
  upDown(2,t);
  pasitos(4,t);
  lateral_fuerte(0,t);
  lateral_fuerte(1,t);
  upDown(2,t);
  
  patada(t*2);
  pasitos(2,t);
  patada(t*2);
  pasitos(2,t);
  swing(2,t*2);
  pasitos(4,t);
  
  for (int i=0; i<4; i++){
    lateral_fuerte(0,t);
    lateral_fuerte(1,t);
    lateral_fuerte(0,t/2);
    lateral_fuerte(1,t/2);
    lateral_fuerte(0,t/2);
  delay(t/2);
  }
  
  pasitos(6,t);
  delay(t);
  pasitos(1,t);
  delay(t/2);
  pasitos(3,t);
  delay(t/2);
  swing(4,t);
  
  twist(2,t/2);
  delay(t/2);
  twist(2,t/2);
  delay(t/2);
  
  drunk(t*2);
  drunk(t/2);
  drunk(t*2);
  delay(t/2);
  walk(1,t);
  backyard(1,t);
  
  servo[0].SetPosition(110);
  servo[1].SetPosition(130);
  delay(t);
  
  crusaito(3,t);
  crusaito(1,2*t);
  upDown(1,t*2);
  upDown(2,t/2);
  
  kickLeft(t/2);
  kickRight(t/2);
  moonWalkLeft(1,t*2);
  moonWalkLeft(2,t);
  moonWalkRight(1,t*2);
  moonWalkRight(2,t);
  
  walk(4,t);
  backyard(4,t);
  
  lateral_fuerte(0,t);
  lateral_fuerte(0,t);
  lateral_fuerte(1,t);
  lateral_fuerte(1,t);
  walk(2,t);
  backyard(2,t);
  
  pasitos(6,t*2);
  swing(1,t);
  upDown(1,t);
  delay(t);
  upDown(6,t);
  delay(t);
  
  for (int i=0;i<4;i++){
    lateral_fuerte(0,t);
    lateral_fuerte(1,t);
  }
  
  delay(t);
  for (int i=0;i<7;i++){
    pasitos(2,t);
    swing(2,t);
  }
  
  pasitos(1,t);
  crusaito(1,t*2);
  upDown(1,t);
  
  delay(2000);
  

}

////////////////////////////////////////////////////////////////////////////////////////
//////////////////////////////////FUNCIONES DE CONTROL//////////////////////////////////
////////////////////////////////////////////////////////////////////////////////////////

void oscillate(int A[N_SERVOS], int O[N_SERVOS], int T, double phase_diff[N_SERVOS]){
  for (int i=0; i<4; i++) {
    servo[i].SetO(O[i]);
    servo[i].SetA(A[i]);
    servo[i].SetT(T);
    servo[i].SetPh(phase_diff[i]);
  }
  double ref=millis();
   for (double x=ref; x<T+ref; x=millis()){
     for (int i=0; i<4; i++){
        servo[i].refresh();
     }
  }
}

unsigned long final_time;
unsigned long interval_time;
int oneTime;
int iteration;
float increment[N_SERVOS]; 
int oldPosition[]={90,90,90,90};

void moveNServos(int time, int  newPosition[]){
  for(int i=0;i<N_SERVOS;i++)	increment[i] = ((newPosition[i])-oldPosition[i])/(time/INTERVALTIME);
  
  final_time =  millis() + time; 
  
  iteration = 1; 
  while(millis() < final_time){ //Javi del futuro cambia esto  
      interval_time = millis()+INTERVALTIME;  
      
      oneTime=0;      
      while(millis()<interval_time){	  
          if(oneTime<1){ 
              for(int i=0;i<N_SERVOS;i++){
                  servo[i].SetPosition(oldPosition[i] + (iteration * increment[i]));
              }			
              iteration++;
              oneTime++;
          }
      }     
  }   

  for(int i=0;i<N_SERVOS;i++){	
    oldPosition[i] = newPosition[i];
  }   
}


//////////////////////////////////////////////////////////////////////////////
////////////////////////////////PASOS DE BAILE////////////////////////////////
//////////////////////////////////////////////////////////////////////////////

void pasitos(int steps, int tempo){
  int move1[4] = {90,120,60,60};
  int move2[4] = {90,90,90,90};
  int move3[4] = {60,90,120,120};
  int move4[4] = {90,90,90,90};
  
  for(int i=0; i<steps; i++){
    pause=millis();
    moveNServos(tempo*0.25,move1);
    moveNServos(tempo*0.25,move2);
    moveNServos(tempo*0.25,move3);
    moveNServos(tempo*0.25,move4);
    while(millis()<(pause+t));
  }
}

void patada (int tempo){
  for(int i=0;i<4;i++) servo[i].SetPosition(90);
  servo[0].SetPosition(115);
  servo[1].SetPosition(120);
  delay(tempo/4);
  servo[0].SetPosition(115);
  servo[1].SetPosition(70);
  delay(tempo/4);
  servo[0].SetPosition(100);
  servo[1].SetPosition(80);
  delay(tempo/4);
  servo[0].SetPosition(90);
  servo[1].SetPosition(90);
  delay(tempo/4);
}

void twist(int steps, int tempo){
  int move1[4] = {90,90,50,130};
  int move2[4] = {90,90,90,90};

    
  for(int x=0; x<steps; x++){ 
      pause=millis();
      moveNServos(tempo*0.1,move1);
      moveNServos(tempo*0.1,move2);
      while(millis()<(pause+tempo));
  }
}

void reverencia1 (int steps, int tempo){
  int move1[4] = {130,50,90,90};
  int move2[4] = {90,90,90,90};
    
  for(int x=0; x<steps; x++){ 
      pause=millis();
      for(int i=0;i<4;i++) servo[i].SetPosition(90);
      moveNServos(tempo*0.3,move1);
      delay(tempo*0.2);
      moveNServos(tempo*0.3,move2);
      while(millis()<(pause+tempo));
  }
}

void reverencia2 (int steps, int tempo){
  int move1[4] = {130,50,90,90};
  int move2[4] = {130,50,60,120};
  int move3[4] = {90,90,90,90};

    
  for(int x=0; x<steps; x++){ 
      pause=millis();
      for(int i=0;i<4;i++) servo[i].SetPosition(90);
      delay(tempo*0.2);
      moveNServos(tempo*0.05,move1);
      moveNServos(tempo*0.05,move2);
      moveNServos(tempo*0.05,move1);
      moveNServos(tempo*0.05,move2);
      delay(tempo*0.2);
      moveNServos(tempo*0.1,move3);
      while(millis()<(pause+tempo));
  }
}

void saludo(int steps, int tempo){
  int move1[4] = {60,60,90,90};
  int move2[4] = {120,60,90,90};
    
  for(int x=0; x<steps; x++){ 
      pause=millis();
      for(int i=0;i<4;i++) servo[i].SetPosition(90);
      moveNServos(tempo*0.25,move1);
      moveNServos(tempo*0.25,move2);
      moveNServos(tempo*0.25,move1);
      moveNServos(tempo*0.25,move2);
      while(millis()<(pause+tempo));
  }
}

void upDown(int steps, int tempo){
  int move1[4] = {50,130,90,90};
  int move2[4] = {90,90,90,90};
    
  for(int x=0; x<steps; x++){ 
      pause=millis();
      moveNServos(tempo*0.2,move1);
      delay(tempo*0.4);
      moveNServos(tempo*0.2,move2);
      while(millis()<(pause+tempo));
  }
}

void lateral_fuerte(boolean side, int tempo){
  
  for(int i=0;i<4;i++) servo[i].SetPosition(90);
  if (side) servo[0].SetPosition(40);
  else servo[1].SetPosition(140);
  delay(tempo/2);
  servo[0].SetPosition(90);
  servo[1].SetPosition(90);
  delay(tempo/2);

}

void run(int steps, int T){
    int A[4]= {10, 10, 10, 10};
    int O[4] = {0, 0, 0, 0};
    double phase_diff[4] = {DEG2RAD(0), DEG2RAD(0), DEG2RAD(90), DEG2RAD(90)}; 
    
    for(int i=0;i<steps;i++)oscillate(A,O, T, phase_diff);
}

void drunk (int tempo){
  
  pause=millis();
  
  int move1[] = {60,70,90,90};
  int move2[] = {110,120,90,90};
  int move3[] = {60,70,90,90};
  int move4[] = {110,120,90,90};
  int move5[] = {90,90,90,90};
  
  moveNServos(tempo*0.235,move1);
  moveNServos(tempo*0.235,move2);
  moveNServos(tempo*0.235,move3);
  moveNServos(tempo*0.235,move4);
  moveNServos(tempo*0.06,move5);
  while(millis()<(pause+tempo));

}

void kickLeft(int tempo){
  for(int i=0;i<4;i++) servo[i].SetPosition(90);
  delay(tempo);
  servo[0].SetPosition(50); //pie derecho
  servo[1].SetPosition(60); //pie izquiero
  delay(tempo);
  servo[0].SetPosition(80); //pie derecho
  servo[1].SetPosition(60); //pie izquiero
  delay(tempo/4);
  servo[0].SetPosition(40); //pie derecho
  servo[1].SetPosition(60); //pie izquiero
  delay(tempo/4);
  servo[0].SetPosition(80); //pie derecho
  servo[1].SetPosition(60); //pie izquiero
  delay(tempo/4);
  servo[0].SetPosition(40); //pie derecho
  servo[1].SetPosition(60); //pie izquiero
  delay(tempo/4);
  servo[0].SetPosition(80); //pie derecho
  servo[1].SetPosition(60); //pie izquiero
  delay(tempo);
}

void kickRight(int tempo){
for(int i=0;i<4;i++) servo[i].SetPosition(90);
  delay(tempo);
  servo[0].SetPosition(120); //pie derecho
  servo[1].SetPosition(130); //pie izquiero
  delay(tempo);
  servo[0].SetPosition(120); //pie derecho
  servo[1].SetPosition(100); //pie izquiero
  delay(tempo/4);
  servo[0].SetPosition(120); //pie derecho
  servo[1].SetPosition(140); //pie izquiero
  delay(tempo/4);
  servo[0].SetPosition(120); //pie derecho
  servo[1].SetPosition(80); //pie izquiero
  delay(tempo/4);
  servo[0].SetPosition(120); //pie derecho
  servo[1].SetPosition(140); //pie izquiero
  delay(tempo/4);
  servo[0].SetPosition(120); //pie derecho
  servo[1].SetPosition(100); //pie izquiero
  delay(tempo);
}

void walk(int steps, int T){
    int A[4]= {15, 15, 30, 30};
    int O[4] = {0, 0, 0, 0};
    double phase_diff[4] = {DEG2RAD(0), DEG2RAD(0), DEG2RAD(90), DEG2RAD(90)};
    
    for(int i=0;i<steps;i++)oscillate(A,O, T, phase_diff);
}

void backyard(int steps, int T){
    int A[4]= {15, 15, 30, 30};
    int O[4] = {0, 0, 0, 0};
    double phase_diff[4] = {DEG2RAD(0), DEG2RAD(0), DEG2RAD(-90), DEG2RAD(-90)}; 
    
    for(int i=0;i<steps;i++)oscillate(A,O, T, phase_diff);
}

void moonWalkRight(int steps, int T){
    int A[4]= {25, 25, 0, 0};
    int O[4] = {-15 ,15, 0, 0};
    double phase_diff[4] = {DEG2RAD(0), DEG2RAD(180 + 120), DEG2RAD(90), DEG2RAD(90)}; 
    
    for(int i=0;i<steps;i++)oscillate(A,O, T, phase_diff);
}

void moonWalkLeft(int steps, int T){
    int A[4]= {25, 25, 0, 0};
    int O[4] = {-15, 15, 0, 0};
    double phase_diff[4] = {DEG2RAD(0), DEG2RAD(180 - 120), DEG2RAD(90), DEG2RAD(90)}; 
    
    for(int i=0;i<steps;i++)oscillate(A,O, T, phase_diff);
}

void crusaito(int steps, int T){
    int A[4]= {25, 25, 30, 30};
    int O[4] = {- 15, 15, 0, 0};
    double phase_diff[4] = {DEG2RAD(0), DEG2RAD(180 + 120), DEG2RAD(90), DEG2RAD(90)}; 
    
    for(int i=0;i<steps;i++)oscillate(A,O, T, phase_diff);
}

void swing(int steps, int T){
    int A[4]= {25, 25, 0, 0};
    int O[4] = {-15, 15, 0, 0};
    double phase_diff[4] = {DEG2RAD(0), DEG2RAD(0), DEG2RAD(90), DEG2RAD(90)};
    
    for(int i=0;i<steps;i++)oscillate(A,O, T, phase_diff);
}

void flapping(int steps, int T){
    int A[4]= {15, 15, 8, 8};
    int O[4] = {-A[0], A[1], 0, 0};
    double phase_diff[4] = {DEG2RAD(0), DEG2RAD(180), DEG2RAD(90), DEG2RAD(-90)};
    
    for(int i=0;i<steps;i++)oscillate(A,O, T, phase_diff);
}

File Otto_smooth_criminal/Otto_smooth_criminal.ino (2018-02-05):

//----------------------------------------------------------------
//-- Otto Dance smooth criminal by Michael Jackson
//-- Released under a GPL licencse (http://ottodiy.com)
//-- Originally made for Zowi project remake for Otto DIY
//-- Authors:  Javier Isabel:  javier.isabel@bq.com
//--           Juan Gonzalez (obijuan): juan.gonzalez@bq.com
//-----------------------------------------------------------------
#include <Servo.h>
#include <Oscillator.h>
#include <EEPROM.h>

#define N_SERVOS 4
//-- First step: Configure the pins where the servos are attached
/*
         --------------- 
        |     O   O     |
        |---------------|
YR 3==> |               | <== YL 2
         --------------- 
            ||     ||
            ||     ||
RR 5==>   -----   ------  <== RL 4
         |-----   ------|
*/
#define EEPROM_TRIM false 
// Activate to take callibration data from internal memory
#define TRIM_RR 7
#define TRIM_RL 4
#define TRIM_YR  4
#define TRIM_YL -7
//OTTO.setTrims(-7,-4,-4,7);

#define PIN_RR 5
#define PIN_RL 4
#define PIN_YR 3
#define PIN_YL 2

#define INTERVALTIME 10.0 

Oscillator servo[N_SERVOS];

void goingUp(int tempo);
void drunk (int tempo);
void noGravity(int tempo);
void kickLeft(int tempo);
void kickRight(int tempo);
void run(int steps, int T=500);
void walk(int steps, int T=1000);
void backyard(int steps, int T=3000);
void backyardSlow(int steps, int T=5000);
void turnLeft(int steps, int T=3000);
void turnRight(int steps, int T=3000);
void moonWalkLeft(int steps, int T=1000);
void moonWalkRight(int steps, int T=1000);
void crusaito(int steps, int T=1000);
void swing(int steps, int T=1000);
void upDown(int steps, int T=1000);
void flapping(int steps, int T=1000);

void setup()
{
  Serial.begin(19200);
  
  servo[0].attach(PIN_RR);
  servo[1].attach(PIN_RL);
  servo[2].attach(PIN_YR);
  servo[3].attach(PIN_YL);
  
  //EEPROM.write(0,TRIM_RR);
  //EEPROM.write(1,TRIM_RL);
  //EEPROM.write(2,TRIM_YR);
  //EEPROM.write(3,TRIM_YL);
  
  int trim;
  
  if(EEPROM_TRIM){
    for(int x=0;x<4;x++){
      trim=EEPROM.read(x);
      if(trim>128)trim=trim-256;
      Serial.print("TRIM ");
      Serial.print(x);
      Serial.print(" en ");
      Serial.println(trim);
      servo[x].SetTrim(trim);
    }
  }
  else{
    servo[0].SetTrim(TRIM_RR);
    servo[1].SetTrim(TRIM_RL);
    servo[2].SetTrim(TRIM_YR);
    servo[3].SetTrim(TRIM_YL);
  }
  
  for(int i=0;i<4;i++) servo[i].SetPosition(90);
}

// TEMPO: 121 BPM
int t=495;
double pause=0;

void loop()
{
 // if(Serial.available()){
  //  char init = Serial.read();
   // if (init=='X'){
   //   delay(4000); //3000 - 4500
   
dance();


//for(int i=0;i<4;i++) servo[i].SetPosition(90);

      
          for(int i=0;i<4;i++) servo[i].SetPosition(90);
   // }
 // }
}

void dance(){
  primera_parte();
  segunda_parte();
  moonWalkLeft(4,t*2);
  moonWalkRight(4,t*2);
  moonWalkLeft(4,t*2);
  moonWalkRight(4,t*2);
  primera_parte(); 
  crusaito(1,t*8);
  crusaito(1,t*7);

  for (int i=0; i<16; i++){
    flapping(1,t/4);
    delay(3*t/4);
  }
 
  moonWalkRight(4,t*2);
  moonWalkLeft(4,t*2);
  moonWalkRight(4,t*2);
  moonWalkLeft(4,t*2);

  drunk(t*4);
  drunk(t*4);
  drunk(t*4);
  drunk(t*4);
  kickLeft(t);
  kickRight(t);
  drunk(t*8);
  drunk(t*4);
  drunk(t/2);
  delay(t*4); 

  drunk(t/2);

  delay(t*4); 
  walk(2,t*2);
  backyard(2,t*2);
  goingUp(t*2);
  goingUp(t*1);
  noGravity(t*2);
  crusaito(1,t*2);
  crusaito(1,t*8);
  crusaito(1,t*2);
  crusaito(1,t*8);
  crusaito(1,t*2);
  crusaito(1,t*3);

  delay(t);
  primera_parte();
    for (int i=0; i<32; i++){
    flapping(1,t/2);
    delay(t/2);
  }
  
  for(int i=0;i<4;i++) servo[i].SetPosition(90);
}




////////////////////////////////////////////////////////////////////////////////////////
//////////////////////////////////FUNCIONES DE CONTROL//////////////////////////////////
////////////////////////////////////////////////////////////////////////////////////////

void oscillate(int A[N_SERVOS], int O[N_SERVOS], int T, double phase_diff[N_SERVOS]){
  for (int i=0; i<4; i++) {
    servo[i].SetO(O[i]);
    servo[i].SetA(A[i]);
    servo[i].SetT(T);
    servo[i].SetPh(phase_diff[i]);
  }
  double ref=millis();
   for (double x=ref; x<T+ref; x=millis()){
     for (int i=0; i<4; i++){
        servo[i].refresh();
     }
  }
}

unsigned long final_time;
unsigned long interval_time;
int oneTime;
int iteration;
float increment[N_SERVOS]; 
int oldPosition[]={90,90,90,90};

void moveNServos(int time, int  newPosition[]){
  for(int i=0;i<N_SERVOS;i++)	increment[i] = ((newPosition[i])-oldPosition[i])/(time/INTERVALTIME);
  
  final_time =  millis() + time; 
  
  iteration = 1; 
  while(millis() < final_time){ //Javi del futuro cambia esto  
      interval_time = millis()+INTERVALTIME;  
      
      oneTime=0;      
      while(millis()<interval_time){	  
          if(oneTime<1){ 
              for(int i=0;i<N_SERVOS;i++){
                  servo[i].SetPosition(oldPosition[i] + (iteration * increment[i]));
              }			
              iteration++;
              oneTime++;
          }
      }     
  }   

  for(int i=0;i<N_SERVOS;i++){	
    oldPosition[i] = newPosition[i];
  }   
}


//////////////////////////////////////////////////////////////////////////////
////////////////////////////////PASOS DE BAILE////////////////////////////////
//////////////////////////////////////////////////////////////////////////////

void goingUp(int tempo){
  
      pause=millis();
      for(int i=0;i<4;i++) servo[i].SetPosition(90);
      delay(tempo);
      servo[0].SetPosition(80);
      servo[1].SetPosition(100);
      delay(tempo);
      servo[0].SetPosition(70);
      servo[1].SetPosition(110);
      delay(tempo);
      servo[0].SetPosition(60);
      servo[1].SetPosition(120);
      delay(tempo);
      servo[0].SetPosition(50);
      servo[1].SetPosition(130);
      delay(tempo);
      servo[0].SetPosition(40);
      servo[1].SetPosition(140);
      delay(tempo);
      servo[0].SetPosition(30);
      servo[1].SetPosition(150);
      delay(tempo);
      servo[0].SetPosition(20);
      servo[1].SetPosition(160);
      delay(tempo);
      
      while(millis()<pause+8*t);

}

void primera_parte(){
  
  int move1[4] = {60,120,90,90};
  int move2[4] = {90,90,90,90};
  int move3[4] = {40,140,90,90};
  
  for(int x=0; x<3; x++){
    for(int i=0; i<3; i++){
      lateral_fuerte(1,t/2);
      lateral_fuerte(0,t/4);
      lateral_fuerte(1,t/4);
      delay(t);
    }
  
    pause=millis();
    for(int i=0;i<4;i++) servo[i].SetPosition(90);
    moveNServos(t*0.4,move1);
    moveNServos(t*0.4,move2);
    while(millis()<(pause+t*2));
  }
  
  for(int i=0; i<2; i++){
    lateral_fuerte(1,t/2);
    lateral_fuerte(0,t/4);
    lateral_fuerte(1,t/4);
    delay(t);
  }
    
  pause=millis();
  for(int i=0;i<4;i++) servo[i].SetPosition(90);
  crusaito(1,t*1.4);
  moveNServos(t*1,move3);
  for(int i=0;i<4;i++) servo[i].SetPosition(90);
  while(millis()<(pause+t*4));
}
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

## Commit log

2016-09-22 snap merged
    [OTTO_head_v2_merged.stl]
2016-09-26 Version 3
    Snap feature improved, added space for switch and buzzer
    [OTTO_body_v3.stl, OTTO_head_v3.stl, OTTO_leg_v3.stl]
2016-10-01 Added zip files for the libraries
    So that they can be imported to Arduino via Sketch -> Include library ->
    Add zip file library
2016-10-25 battery check deleted
2016-10-31 Pin buzzer changed from A2 to 10
    buzzer pin for Otto schematic
2016-12-29 updated version 3
    New leg and foot design and instruction manual with Arduino part
    [OTTO_footL_v3.stl, OTTO_footR_v3.stl, OTTO_leg_v4.stl]
2016-12-29 Move functions to play within Arduino
2017-02-04 Battery alarm level canceled
2017-03-03 Update HC06_BT_config.ino
    Improved comments on the code.
    Corrected default baudrate for HC-06 module (9600)
    Changed Arduino´s onboard LED (Digital 13)
2017-05-16 new dance, calibration and home for servos
2017-06-08 New instruction manual with Arduino
    Printable in A6 with details of how to code Otto now in
2017-06-21 added the pins for the us sensor
    we need to tell OTTO where the trigger and echo pins are
2017-06-21 3d print files with Pedro legs
    Pedro make a great improvement for the legs, the original version is also there just in case :)
    [OTTO_body_Pedro.stl, OTTO_body_v3.stl, OTTO_feet_Pedro.stl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]
2017-09-05 Update OTTO_avoid.ino
    The buzzer is initialized on pin -1, but should be on pin 10
2017-10-18 Create OTTO_TouchSensor
    A simple program to enjoy with OTTO and his touch sensor
2017-12-11 name of motors
2018-02-05 3D update
    legs and feet
    [OttoDIY_CUSTOM.scad, OttoDIY_Feet_v05.stl, OttoDIY_Legs_v05.stl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]
2018-02-05 assembly instructions v06
2018-03-11 Add LedMatrix library
2018-04-09 Revert "Update Otto.h"
    This reverts commit 7fce5705e14b92c6b38b903a7c4f978b2783aed6.
    There is a lot of code in the Otto library that is dependent on the LedMatrix library so of course removing this #include directive causes it to no longer compile:
    In file included from C:\Users\per\Desktop\DIY-master\Otto_avoid\Otto_avoid.ino:10:0:
    E:\electronics\arduino\libraries\Otto/Otto.h:97:5: error: 'LedMatrix' does not name a type
    LedMatrix ledmatrix;
2018-05-10 design by Lucid Wolf
    https://www.thingiverse.com/thing:2495022
    [OttoDIY_AngryEyes.stl, OttoDIY_Bunny.stl, OttoDIY_Elf.stl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]
2018-05-11 sound pin to 13
2018-06-28 Halloween
    #Ottoween
    [Otto_BoneyHands.stl, Otto_Halloween_remix_Tinyplans_minion.stl, Otto_Horns.stl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]
2018-09-19 3D STL update
    [OttoDIY+_Leg_v07.stl, OttoDIY+_body_v07.stl, OttoDIY+_foot_v06.stl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]
2018-10-24 pin 13
2019-04-20 Add esp32 support
2019-07-30 arduino 1.8.5. version
2019-09-23 Interactive calibration for Otto DIY.
2020-04-17 Make up-to-date with latest version of ESP32Servo
2020-10-28 Cambios y arreglos importantes
    Cambiada indentacion de dos espacios, a una tabulacion
    Codigo arreglado para que compile:
    * Añadida definicion de algunas funciones
    * Re-acomodado codigo
    Removido codigo innecesario
    Mas correcciones de indentacion
    Añadidos algunos comentarios
    [Otto_smooth_criminal.ino]

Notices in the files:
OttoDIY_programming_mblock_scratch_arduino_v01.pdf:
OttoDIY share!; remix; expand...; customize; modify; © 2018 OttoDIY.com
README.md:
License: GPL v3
